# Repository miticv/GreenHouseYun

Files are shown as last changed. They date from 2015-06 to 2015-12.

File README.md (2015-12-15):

# GreenHouseYun
Green House Controller App using Arduino Yun

Command for getting public IP from network interface eth1:
```bash
LANG=c ifconfig eth1 | grep "inet addr" | awk -F: '{print $2}' | awk '{print $1}'
```
or if not sure what is the interface, list all interfaces:
```bash
LANG=c ifconfig |grep -B1 "inet addr" |awk '{ if ( $1 == "inet" ) { print $2 } else if ( $2 == "Link" ) { printf "%s:" ,$1 } }' |awk -F: '{ print $1 ": " $3 }'
```

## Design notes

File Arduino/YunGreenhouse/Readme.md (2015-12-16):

Ino is using following pins:
##ANALOG:
* 0 - read light

##DIGITAL:
* 2 - One Wire (for temperature sensors)
* 7 - Pin to reboot the Yun
* 10 - DHT Temp/Humidity Sensor (DHT22)
* 13 - built in red light on the YUN (signal when arduino is ready)

##Website: 
* http://192.168.1.35/sd/

##Arduino APIs:
It is accepting only calls from Linux box on: http://127.0.0.1:5555/

* temp  (reads temperature from DHT sensor)
* temps (reads all temperatures from sensors)
* light (reads light sensor)
* err (show last error)
* veggielightoff 
* veggielighton
* lightoff
* lighton
* boot (reboots the arduino)
* data (gets all sensor data back)

##APIs:

accepts "from" and "to"

* http://192.168.1.35/sd/api.php?action=get_info_log
* http://192.168.1.35/sd/api.php?action=get_error_log

accepts "from", "to" and "freq"

* http://192.168.1.35/sd/api.php?action=get_sensor_log
* 

* http://192.168.1.35/sd/api.php?action=light_off
* http://192.168.1.35/sd/api.php?action=light_on
* http://192.168.1.35/sd/api.php?action=get_uptime
* http://192.168.1.35/sd/api.php?action=get_sensor_data
* http://192.168.1.35/sd/api.php?action=get_sensor_definitions
* http://192.168.1.35/sd/api.php?action=get_sensor_and_uptime_data
* http://192.168.1.35/sd/api.php?action=reset_arduino
* http://192.168.1.35/sd/api.php?action=reset_yun

##BASIC WRT

* ssh root@ip.address.of.the.yun
* mysql -root -p

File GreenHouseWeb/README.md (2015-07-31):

# pluralsight-gulp
You've built your JavaScript application but how do you automate testing, code analysis, running it locally or deploying it? These redundant tasks can consume valuable time and resources. Stop working so hard and take advantage of JavaScript task automation using Gulp to streamline these tasks and give you back more time in the day. Studying this repo can help clarify how Gulp works, jump-start task automation with Gulp, find and resolve issues faster, and be a more productive.

## Requirements

- Install Node
	- on OSX install [home brew](http://brew.sh/) and type `brew install node`
	- on Windows install [chocolatey](https://chocolatey.org/) 
    - Read here for some [tips on Windows](http://jpapa.me/winnode)
    - open command prompt as administrator
        - type `choco install nodejs`
        - type `choco install nodejs.install`
- On OSX you can alleviate the need to run as sudo by [following these instructions](http://jpapa.me/nomoresudo). I highly recommend this step on OSX
- Open terminal
- Type `npm install -g node-inspector bower gulp`

## Quick Start
Prior to taking the course, clone this repo and run the content locally
```bash
$ npm install
$ bower install
$ npm start    (or: $ node src/server/server.js)
```
## Gulp, bower and npm

npm installs server packages( -g installs it globaly)
```bash
  npm install -g gulp bower
```
 list to show all global packages installed:
```bash
  npm list -g --depth=0 
```
--save saves to dependencies in package.json (run time dependencies: angular, bootstrap, ...)
```bash
  npm install --save
```
--save-dev saves in devDEpendencies in package.json (developer dependencies: JSHint, Uglify, Concat...)
```bash
  npm install --save-dev
```
## bower client packages

```bash
npm install -g gulp bower
```
#js
```bash
npm install --save-dev gulp-jscs gulp-jshint yargs gulp-load-plugins gulp-if gulp-print gulp-util jshint-stylish 
```
#css
```bash
npm install --save-dev gulp-less gulp-autoprefixer del gulp-plumber
```
#html
```bash
npm install --save-dev gulp-inject wiredep
```
#Automated starting dev:
```bash
npm install --save-dev gulp-nodemon
```bash

#browser syncing
```bash
npm install --save-dev browser-sync
```

# build

```bash
npm install --save-dev gulp-task-listing gulp-imagemin
```

gulp angular template cache
```bash
npm install --save-dev gulp-minify-html gulp-angular-templatecache

npm install --save-dev gulp-useref

npm install --save-dev gulp-csso gulp-uglify gulp-filter
```

# Angular automated anotation 

Finds code and adds annotation:
```bash
npm install --save-dev gulp-ng-annotate
```
now we can just write: 
```bash
  controller('homeController', function ($scope, greenApiService, NotifierService, $q, $interval) 
```
instead of:
```bash
  controller('homeController', ['$scope', 'greenApiService', 'NotifierService', '$q', '$interval',
                       function ($scope, greenApiService, NotifierService, $q, $interval) 
```
or:
```bash
  controller('homeController', homeController);
 function homeController($scope, greenApiService, NotifierService, $q, $interval) 
```
instead of:
```bash
  controller('homeController', homeController);
  homeController.$inject ['$scope', 'greenApiService', 'NotifierService', '$q', '$interval'];
  function  homeController($scope, greenApiService, NotifierService, $q, $interval) 
```

# revisions

```bash
npm install --save-dev gulp-rev gulp-rev-replace gulp-bump
```

# testing with karma

```bash
npm install --save-dev mocha chai sinon
npm install --save-dev karma karma-chai karma-chai-sinon karma-chrome-launcher karma-coverage karma-growl-reporter karma-mocha karma-phantomjs-launcher karma-sinon mocha-clean sinon-chai phantomjs
npm install --save-dev karma-ie-launcher
```
npm WARN deprecated mocha-clean@0.4.0: Mocha 2.2.5 already shortens stack traces by default.

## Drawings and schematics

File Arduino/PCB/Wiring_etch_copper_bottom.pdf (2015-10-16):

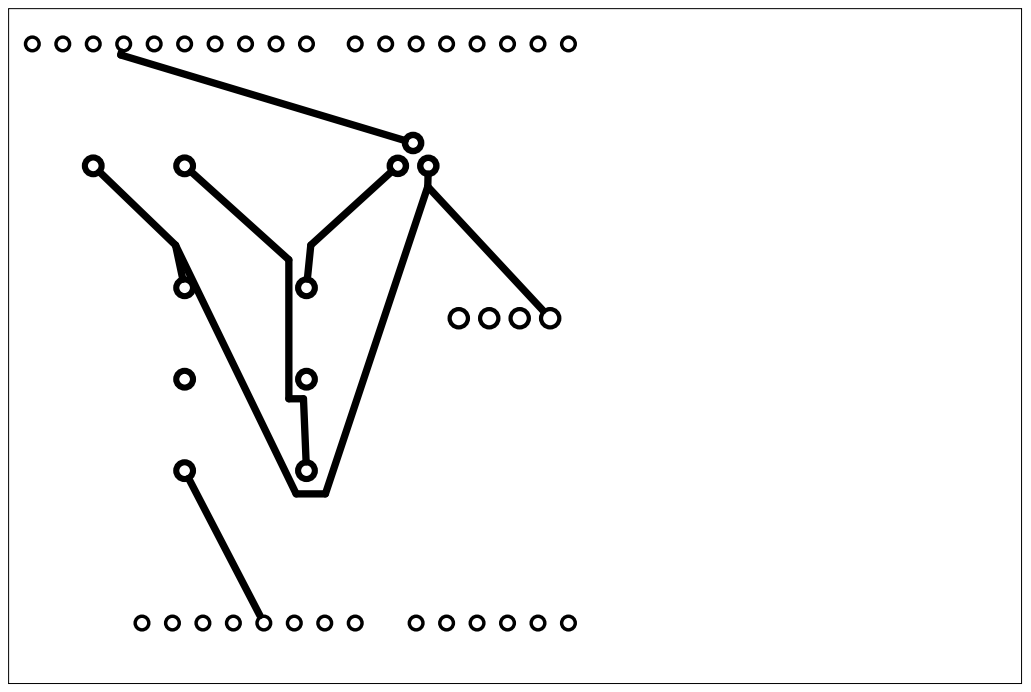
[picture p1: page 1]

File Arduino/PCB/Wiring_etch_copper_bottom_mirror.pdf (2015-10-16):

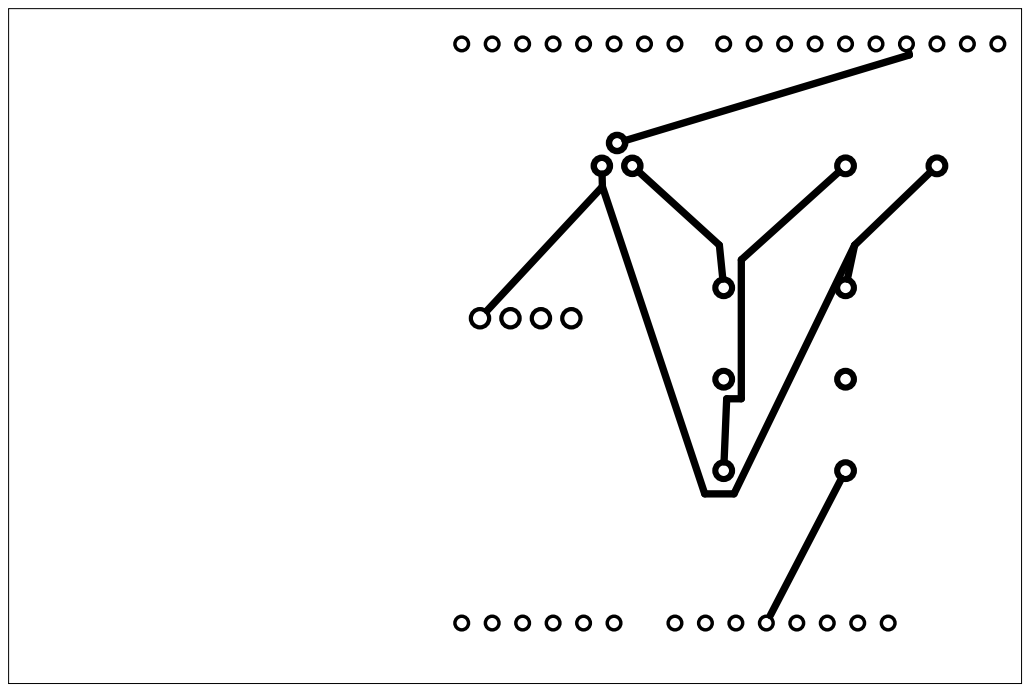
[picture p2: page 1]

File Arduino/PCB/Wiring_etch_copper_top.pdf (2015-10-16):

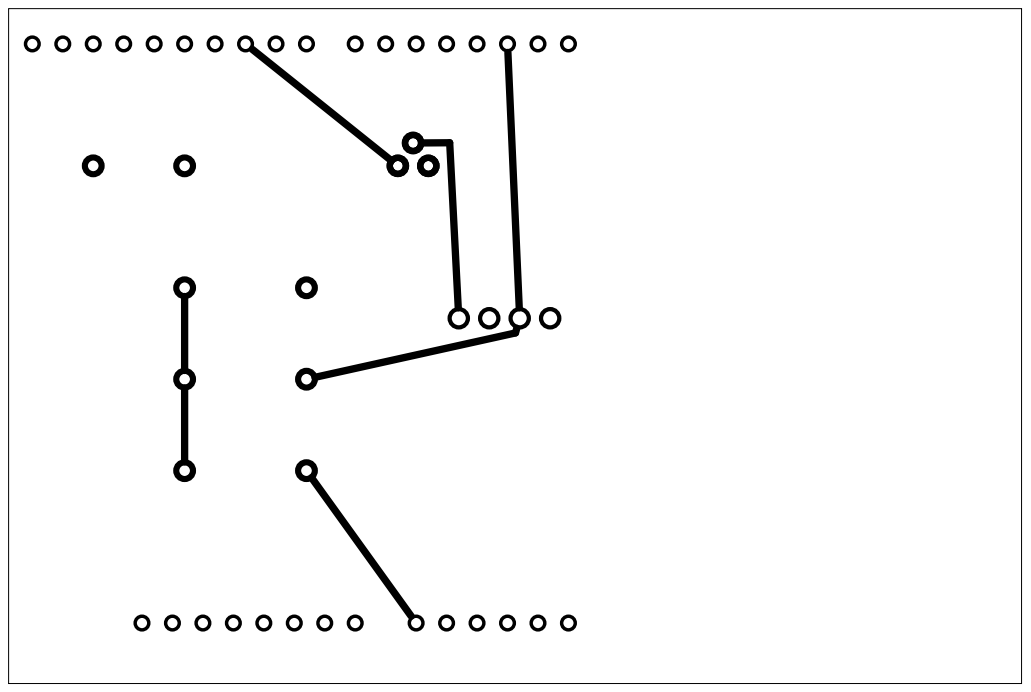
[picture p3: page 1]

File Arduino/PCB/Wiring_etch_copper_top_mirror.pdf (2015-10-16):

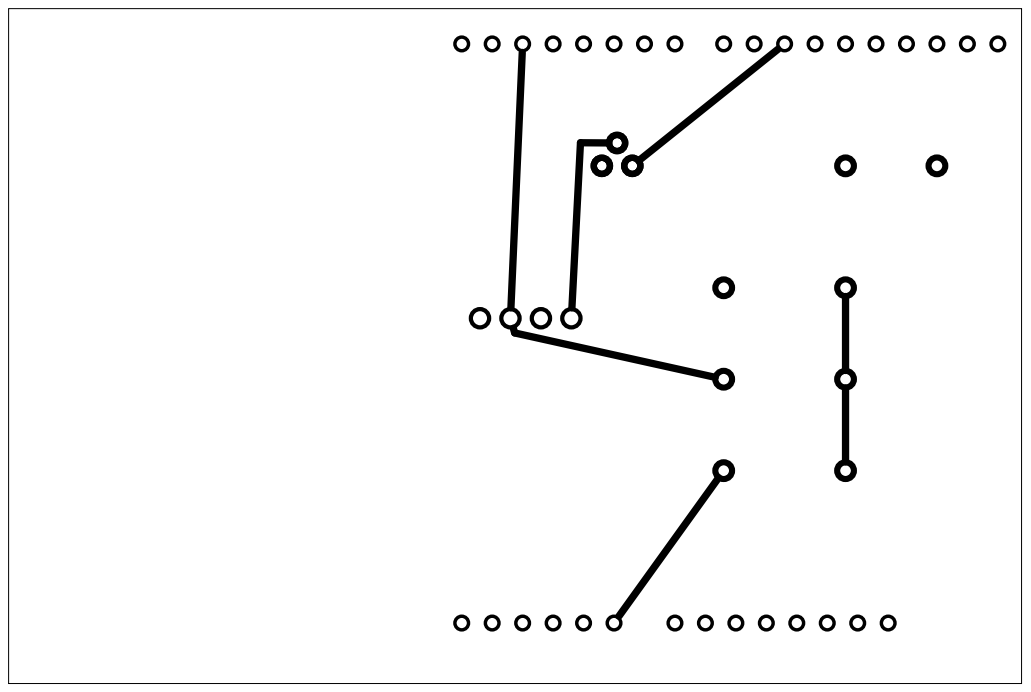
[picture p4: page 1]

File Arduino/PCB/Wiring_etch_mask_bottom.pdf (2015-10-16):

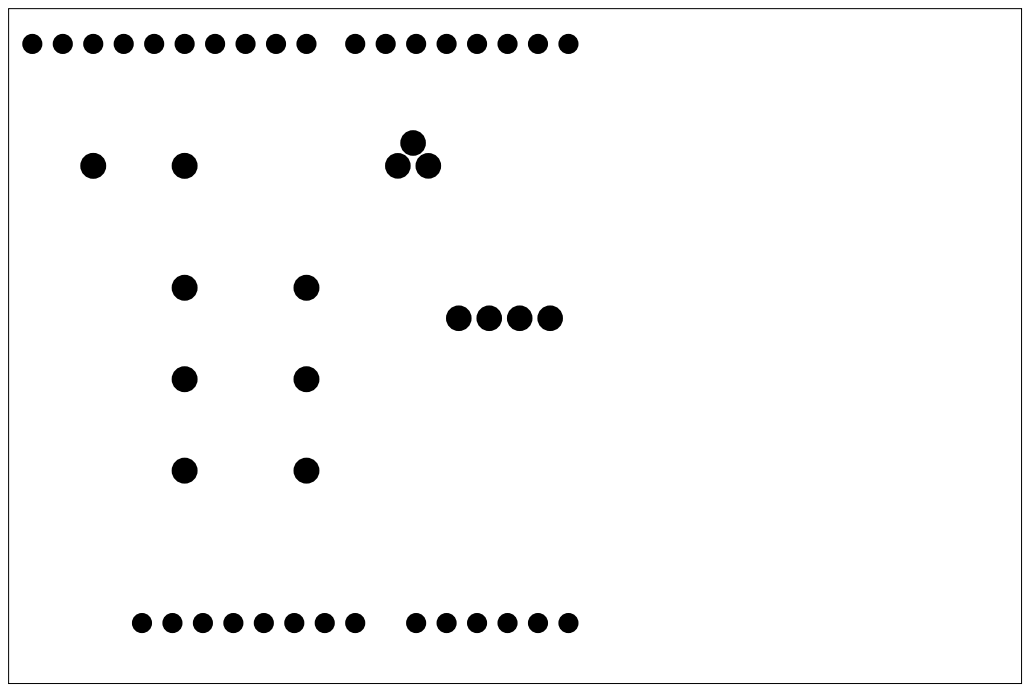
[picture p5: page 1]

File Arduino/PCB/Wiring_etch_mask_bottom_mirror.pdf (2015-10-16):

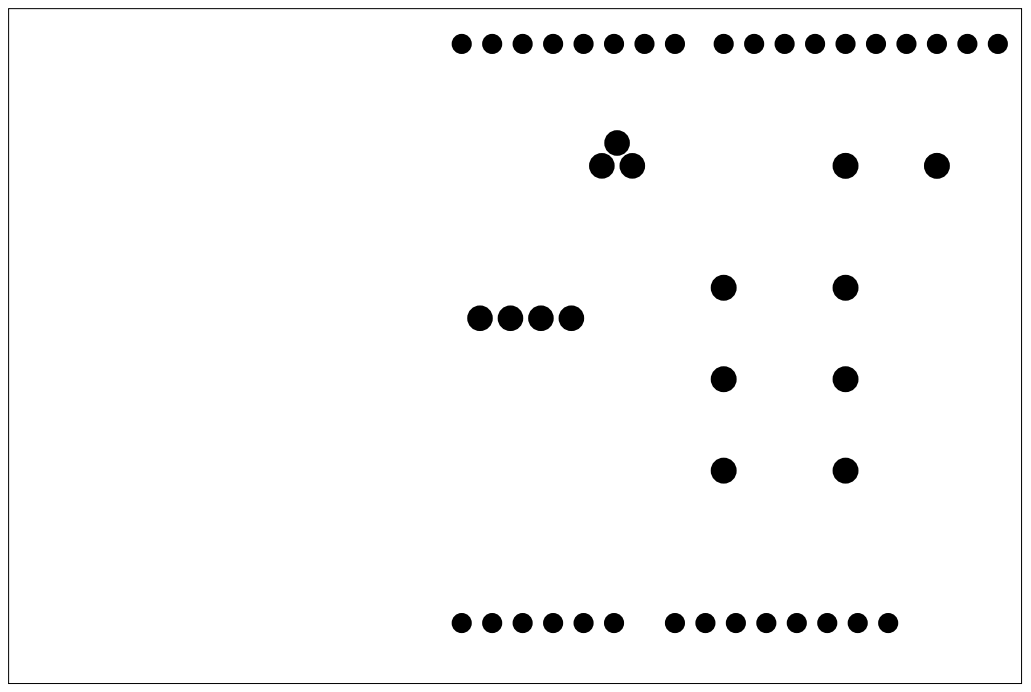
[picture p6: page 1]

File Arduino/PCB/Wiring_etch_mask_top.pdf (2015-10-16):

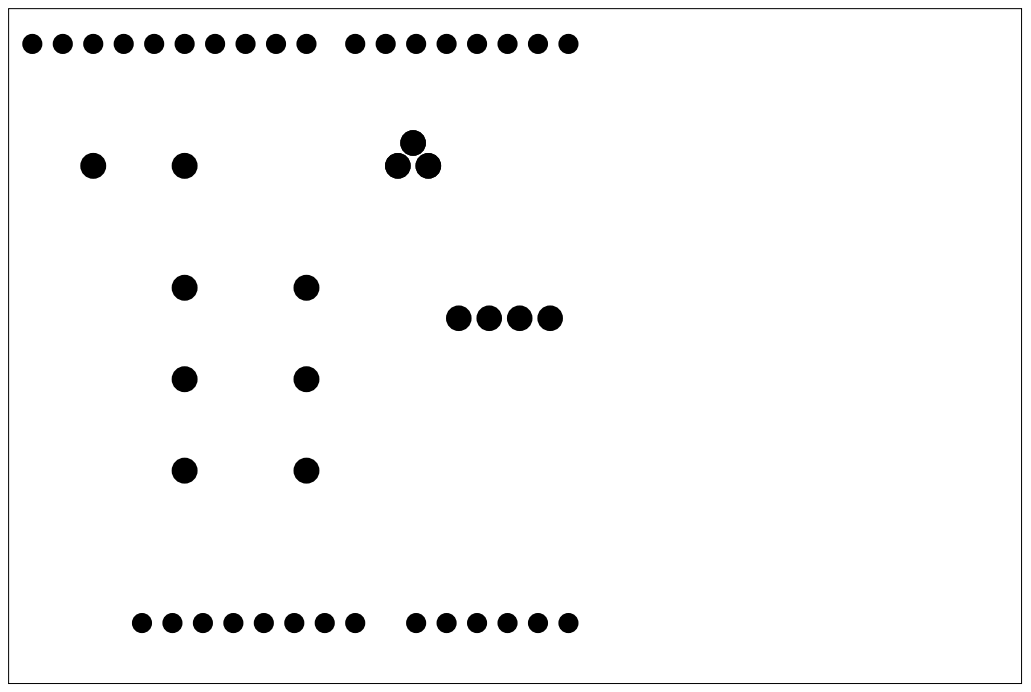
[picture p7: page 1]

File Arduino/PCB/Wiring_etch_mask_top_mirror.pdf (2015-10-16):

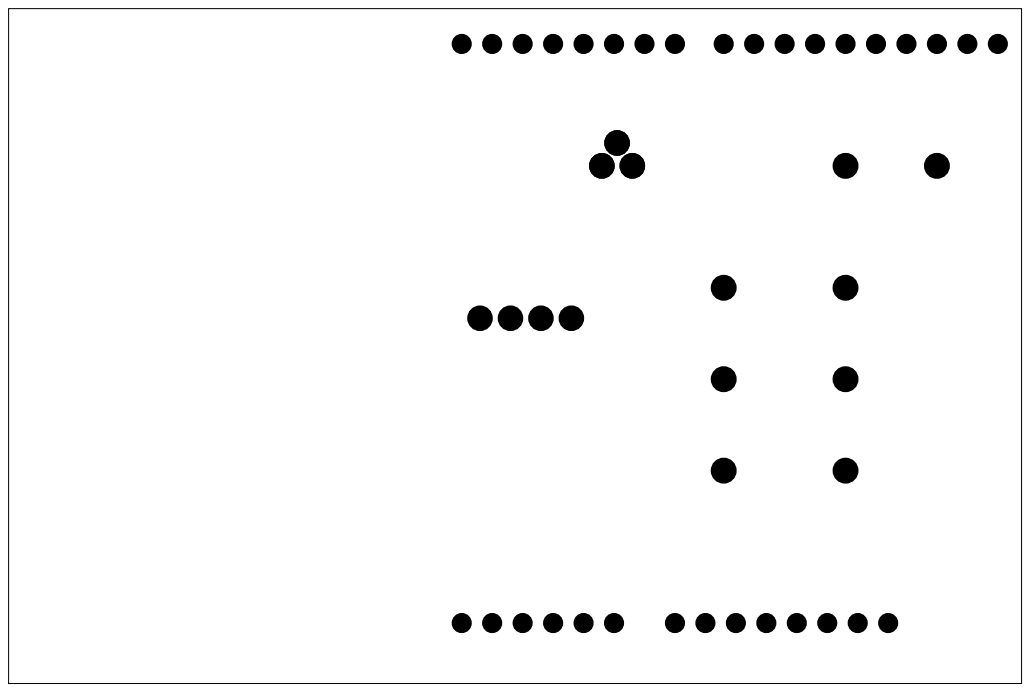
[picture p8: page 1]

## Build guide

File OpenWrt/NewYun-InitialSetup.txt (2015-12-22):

1) do YunSysupgrade:
http://www.arduino.cc/en/Tutorial/YunSysupgrade
- Get SD card (2GB)
- Copy to root the openwrt-ar71xx-generic-yun-16M-squashfs-sysupgrade.bin
- Connect to YUN wifi
- open http://192.168.240.1
- Default password is "arduino"
- Click "RESET" button

2) expand YUN disk space:
http://www.arduino.cc/en/Tutorial/ExpandingYunDiskSpace
- Upload the sketch "YunDiskSpaceExpander.ino" using serial connection
- Open Serial monitor (using NewLine dropdown menu)
- yes (proceed)
- yes (connected to internet)
- yes (partitioning - will loose everything from the SD card)
- 1024 (size in MB for partition)
- When done press YUN RST to reboot

3) check system:
df -h / /mnt/sda1

=================================================================================

1ALT) ALTERNATIVE WITHOUT WEB INTERFACE (with latest linino):
	cd /mnt/sda1
	wget http://download.linino.org/linino_distro/master/latest/openwrt-ar71xx-generic-linino-yun-16M-250k-squashfs-sysupgrade.bin
	sysupgrade -v openwrt-ar71xx-generic-linino-yun-16M-250k-squashfs-sysupgrade.bin
	NOTE:
	above version is not 100% yun compatible better FTP this file to sd card and install that one:
	openwrt-ar71xx-generic-yun-16M-squashfs-sysupgrade.bin
	How to set up ftp? view here https://github.com/miticv/GreenHouseYun/blob/master/OpenWrt/SetUpScript.txt

2ALT) AlTERNATIVE without INO and serial connection:
a)haltIfSDAlreadyOnOverlay 
(should give no results, if it does: Micro SD card is already used as additional Arduino Yun disk space. Nothing to do.)
	mount | grep ^/dev/sda | grep 'on /overlay'
	
b)haltIfInternalFlashIsFull
should give more than 1000 otherwise: You don't have enough disk space to install the utility software. You need to free at least 1MB of Flash memory.\nRetry!
	df / | awk '/rootfs/ {print $4}'
		
c)haltIfSDCardIsNotPresent
(should list - make sure SD card is in "The micro SD card is not available")
	ls /mnt/sda1

d)installSoftware
//make sure you are online:
	opkg update
	opkg install e2fsprogs mkdosfs fdisk rsync

//if Signature check failed.Remove wrong Signature file. then comment #option check_signature from /etc/opkg.conf

e)partitionAndFormatSDCard

//unmount
	umount /dev/sda?
	rm -rf /mnt/sda?

//clears partition table
	dd if=/dev/zero of=/dev/sda bs=4096 count=10

// create the first partition (replace 1024 to how many megs you want for data)
	(echo n; echo p; echo 1; echo; echo +2048M; echo w) | fdisk /dev/sda

//unmount
	umount /dev/sda?
	rm -rf /mnt/sda?

// create the second partition
	(echo n; echo p; echo 2; echo; echo; echo w) | fdisk /dev/sda

//unmount
	umount /dev/sda?
	rm -rf /mnt/sda?

// specify first partition is FAT32
	(echo t; echo 1; echo c; echo w) | fdisk /dev/sda

//unmount
	umount /dev/sda?
	rm -rf /mnt/sda?

// wait 5 sec
//unmount
	umount /dev/sda?
	rm -rf /mnt/sda?

// format the first partition to FAT32
	mkfs.vfat /dev/sda1

// wait 1 sec

// format the second partition to Linux EXT4
	mkfs.ext4 /dev/sda2

f)createArduinoFolder

	mkdir -p /mnt/sda1
	mount /dev/sda1 /mnt/sda1
	mkdir -p /mnt/sda1/arduino/www
//unmount
	umount /dev/sda?
	rm -rf /mnt/sda?

g)copySystemFilesFromYunToSD
	
	mkdir -p /mnt/sda2
	mount /dev/sda2 /mnt/sda2
	rsync -a --exclude=/mnt/ --exclude=/www/sd /overlay/ /mnt/sda2/
//unmount
	umount /dev/sda?
	rm -rf /mnt/sda?

h)enableExtRoot

	uci add fstab mount
	uci set fstab.@mount[0].target=/overlay
	uci set fstab.@mount[0].device=/dev/sda2
	uci set fstab.@mount[0].fstype=ext4
	uci set fstab.@mount[0].enabled=1
	uci set fstab.@mount[0].enabled_fsck=0
	uci set fstab.@mount[0].options=rw,sync,noatime,nodiratime
	uci commit

i) We are done! Now press the YUN RST button to apply the changes.

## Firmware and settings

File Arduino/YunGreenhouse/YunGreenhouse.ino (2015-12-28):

#include <Bridge.h>
#include <YunServer.h>
#include <YunClient.h> 
#include <Process.h>  /* for making OpenWrt linux process requests */

YunServer server;
YunClient client;

/* ##################### temperature humidity ##################### */
#include "DHT.h"
#define DHTPIN 10        // what pin we're connected to DIGITAL


// Uncomment whatever type you're using!
//#define DHTTYPE DHT11   // DHT 11 
#define DHTTYPE DHT22   // DHT 22  (AM2302)
//#define DHTTYPE DHT21   // DHT 21 (AM2301)

// Connect pin 1 (on the left) of the sensor to +5V
// NOTE: If using a board with 3.3V logic like an Arduino Due connect pin 1
// to 3.3V instead of 5V!
// Connect pin 2 of the sensor to whatever your DHTPIN is
// Connect pin 4 (on the right) of the sensor to GROUND
// Connect a 10K resistor from pin 2 (data) to pin 1 (power) of the sensor

// Initialize DHT sensor for normal 16mhz Arduino
DHT dht(DHTPIN, DHTTYPE);
// NOTE: For working with a faster chip, like an Arduino Due or Teensy, you
// might need to increase the threshold for cycle counts considered a 1 or 0.
// You can do this by passing a 3rd parameter for this threshold.  It's a bit
// of fiddling to find the right value, but in general the faster the CPU the
// higher the value.  The default for a 16mhz AVR is a value of 6.  For an
// Arduino Due that runs at 84mhz a value of 30 works.
// Example to initialize DHT sensor for Arduino Due:
//DHT dht(DHTPIN, DHTTYPE, 30);

/* ##################### resetFunc ################################ */
void(*resetFunc) (void) = 0;  //declare reset function @ address 0


/* ##################### temperature libraries ##################### */
#include <OneWire.h>
#include <DallasTemperature.h>

#define ONEWIREPIN 2  // what pin we're connected to DIGITAL
OneWire bus(ONEWIREPIN);
DallasTemperature sensors(&bus);
const int TemperatureDevices = 10;
int numberOfDevices;
DeviceAddress tempSensors[TemperatureDevices];  //DeviceAddress is uint8_t[8]
bool tempSensorsReadable[TemperatureDevices];

/* ############################### boot ########################### */
#define BOOTPIN 7        // what pin we're connected to DIGITAL BOOT (default closed: HIGH)

/* ############################### digital pins ########################### */
#define VEGGIEPIN 6        // what pin we're connected to VEGGIE LIGHT  (default closed: HIGH)
#define LIGHTPIN 5              // what pin we're connected to GreenhouseLight  (default closed: HIGH)
#define BRIDGEREADYPIN 13     ////light up LED 13 as a signal that bridge is ready

/* ############################### analog pins ########################### */
#define LIGHTSENSORPIN 0    //
/* ##################### VARS ##################################### */
// All request will be transfered here
float TempVar[4];
int i;
char errorString[50];
char tempString[100];
char temp;
//char sensorFloatValue[10];
char sensorValue[5];
Process p;
String command;
 
void setup() {
// Bridge startup: 
  // do nothing for 10 seconds (do not interupt booting process):
  delay(10000); 

  pinMode(BOOTPIN, OUTPUT);
  digitalWrite(BOOTPIN, HIGH);

  pinMode(VEGGIEPIN, OUTPUT);
  digitalWrite(VEGGIEPIN, HIGH);

  pinMode(LIGHTPIN, OUTPUT);
  digitalWrite(LIGHTPIN, HIGH);
  
  pinMode(BRIDGEREADYPIN, OUTPUT);
  digitalWrite(BRIDGEREADYPIN, LOW);

  Bridge.begin();

  dht.begin();
  
  sensors.begin();
  SensorsSetUp();
  
  //asks for credentials:
  server.noListenOnLocalhost(); 
  //does not ask for credentials:
  //server.listenOnLocalhost();
  
  server.begin();
  
  //light up LED 13 as a signal that bridge is ready
  digitalWrite(BRIDGEREADYPIN, HIGH);
 
}

void loop() {
  
  // Get clients coming from server
  client = server.accept();
  // There is a new client?
  if (client) {
        // read the command
        getCommand();
        
	clientSendJSON();

	if (command == "temp") {
		ReadDHT();
	}
	else if (command == "temps") {
		ReadTemps();
	}
	else if (command == "light") {
		ReadLight();
	}
	else if (command == "err") {
		ShowLastError();
	}
	else if (command == "veggielightoff") {
		VeggieLight(0);
	}
	else if (command == "veggielighton") {
		VeggieLight(1);
	}
	else if (command == "lightoff") {
		Light(1);
	}
	else if (command == "lighton") {
		Light(0);
	}
  else if (command == "lightflick") {
    if(digitalRead(LIGHTPIN) == HIGH){
        Light(0);
    }else{
        Light(1);
    }
  }
	else if (command == "boot") {
		Reboot();
	}
	else if (command == "data") {
		ReadData();
	}else{
          client.println("{\"error\":\"Invalid command\" }");
        }

    // Close connection and free resources.
    client.stop();
    
  }
  digitalWrite(13, HIGH);
  delay(50); // Poll every 50ms
       
}

void ReadData(){
	client.print("{ \"Light\": ");
	ReadLight();
	client.print(", \"DHT\": ");
	ReadDHT();
	client.print(", \"Temperatures\": ");
	ReadTemps();
	client.print(", \"DigitalPins\": ");
	ReadDigitalPins();

	        client.print(", \"NumberOfTemperatures\": ");
			client.print(numberOfDevices);

//        client.print(", \"Command\": ");
//        client.print("\"");
//        client.print(command);
//        client.print("\"");

	client.print("}");
}

void ReadLight(){

	// Measure light level: LIGHTSENSORPIN
	client.print("{ \"Light\":");
	client.print(analogRead(LIGHTSENSORPIN));
	client.print(", \"Address\": \"Analog");
	client.print(LIGHTSENSORPIN);
	client.print("\"");
	client.print(" }");
}

void ReadDHT(){

	// Reading temperature or humidity takes about 250 milliseconds!
	// Sensor readings may also be up to 2 seconds 'old' (its a very slow sensor)
	TempVar[0] = dht.readHumidity();
	// Read temperature as Celsius
	TempVar[1] = dht.readTemperature();
	// Read temperature as Fahrenheit
	TempVar[2] = dht.readTemperature(true);
	// Check if any reads failed and exit early (to try again).
	if (isnan(TempVar[0]) || isnan(TempVar[1]) || isnan(TempVar[2])) {
		client.print("{\"error\":\"Failed to read from DHT sensor!\"}");
	}
	else{
		// Compute heat index
		// Must send in temp in Fahrenheit!
		TempVar[3] = dht.computeHeatIndex(TempVar[2], TempVar[0]);

		client.print("{ \"HumidityPercent\":");
		client.print(TempVar[0]);
		client.print(", \"TempC\":");
		client.print(TempVar[1]);
		client.print(", \"TempF\":");
		client.print(TempVar[2]);
		client.print(" , \"HeatIndexF\":");
		client.print(TempVar[3]);
		client.print(", \"Address\": \"Digital");
		client.print(DHTPIN);
		client.print("\"");
		client.print("}");

	}
}

void ReadTemps(){

	sensors.requestTemperatures();
	client.print("[");
	for (i = 0; i < numberOfDevices; i++)
	{		
		client.print("{ \"Address\": \"");
		printAddress(tempSensors[i]);
		client.print("\" ,");
		client.print("\"TempC\": ");		
		if (tempSensorsReadable[i]){ 
			TempVar[0] = sensors.getTempC(tempSensors[i]);
			if (TempVar[0] < -100){  //sensor disconnected shows -127
				client.print("-999");
			}
			else{
				client.print(TempVar[0]);
			}			
		}
		else {
			client.print("-999");
		}
		client.print("}");
		if (i != (numberOfDevices - 1)) client.print(", ");
	}
	client.print("]");
}

void ReadDigitalPins(){
	
	client.print("{ ");
	client.print("\"VeggieLight\": { \"value\": ");
	client.print(digitalRead(VEGGIEPIN));
	client.print(", \"Address\": \"Digital");
	client.print(VEGGIEPIN);
	client.print("\" },");

	client.print("\"Light\": {  \"value\":");
	client.print(digitalRead(LIGHTPIN));
	client.print(", \"Address\": \"Digital");
	client.print(LIGHTPIN);
	client.print("\" }");
	client.print("} ");
}

void ShowLastError(){

	client.print("{ \"error\" : \"");
	client.print(errorString);
	client.print("\"}");

}

void Reboot(){
  digitalWrite(BOOTPIN, LOW); //send reboot signal
}

void VeggieLight(uint8_t onoff){
	if (onoff == 0){
		digitalWrite(VEGGIEPIN, LOW);
		client.print("{ \"result\" : \"success veggie light low\" }");
	}
	else {
		digitalWrite(VEGGIEPIN, HIGH);
		client.print("{ \"result\" : \"success  veggie light high\" }");
	}
}

void Light(uint8_t onoff){
	if (onoff == 0){
		digitalWrite(LIGHTPIN, LOW);
		client.print("{ \"result\" : \"success light low\" }");
	}
	else {
		digitalWrite(LIGHTPIN, HIGH);
		client.print("{ \"result\" : \"success light high\" }");
	}
}

void clientSendJSON(){
	client.println("Status: 200");
	client.println("Content-type: application/json");
	client.println();
}

void getCommand(){
        //String command = client.readString();
        int i = 0;
        while(command.indexOf("GET") < 0 || i > 20 ){
                command = client.readStringUntil('\r');
                i++;
        }
        command.trim();        //kill whitespace
        command = command.substring(command.indexOf(" /")+2,command.indexOf(" HTTP"));  //"GET /data HTTP/1.1"
}

void SensorsSetUp(){

	numberOfDevices = sensors.getDeviceCount();

	for (i = 0; i < numberOfDevices; i++)
	{
		strcpy(errorString, "DS18B20 not found: ");
		if (!sensors.getAddress(tempSensors[i], i))
		{
			tempSensorsReadable[i] = false;
			strcat(errorString, itoa(i + 1, sensorValue, 10));
			strcat(errorString, " ");
		}
		else{
			tempSensorsReadable[i] = true;
		}
	}


}

void printAddress(uint8_t* address){

	for (int j = 0; j < 8; j++)
	{
		client.print(address[j], HEX);
		if(j<7) client.print(" ");
	}

}

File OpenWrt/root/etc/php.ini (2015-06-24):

[PHP]

zend.ze1_compatibility_mode = Off

; Language Options

engine = On
;short_open_tag = Off
precision    =  12
y2k_compliance = On
output_buffering = Off
;output_handler =
zlib.output_compression = Off
;zlib.output_compression_level = -1
;zlib.output_handler =
implicit_flush = Off
unserialize_callback_func =
serialize_precision = 100

;open_basedir =
disable_functions =
disable_classes =

; Colors for Syntax Highlighting mode.  Anything that's acceptable in
; <span style="color: ???????"> would work.
;highlight.string  = #DD0000
;highlight.comment = #FF9900
;highlight.keyword = #007700
;highlight.bg      = #FFFFFF
;highlight.default = #0000BB
;highlight.html    = #000000

;ignore_user_abort = On
;realpath_cache_size = 16k
;realpath_cache_ttl = 120

; Miscellaneous

expose_php = On

; Resource Limits

max_execution_time = 30	; Maximum execution time of each script, in seconds.
max_input_time = 60	; Maximum amount of time each script may spend parsing request data.
;max_input_nesting_level = 64
memory_limit = 8M	; Maximum amount of memory a script may consume.

; Error handling and logging

; Error Level Constants:
; E_ALL             - All errors and warnings (includes E_STRICT as of PHP 6.0.0)
; E_ERROR           - fatal run-time errors
; E_RECOVERABLE_ERROR  - almost fatal run-time errors
; E_WARNING         - run-time warnings (non-fatal errors)
; E_PARSE           - compile-time parse errors
; E_NOTICE          - run-time notices (these are warnings which often result
;                     from a bug in your code, but it's possible that it was
;                     intentional (e.g., using an uninitialized variable and
;                     relying on the fact it's automatically initialized to an
;                     empty string)
; E_STRICT			- run-time notices, enable to have PHP suggest changes
;                     to your code which will ensure the best interoperability
;                     and forward compatibility of your code
; E_CORE_ERROR      - fatal errors that occur during PHP's initial startup
; E_CORE_WARNING    - warnings (non-fatal errors) that occur during PHP's
;                     initial startup
; E_COMPILE_ERROR   - fatal compile-time errors
; E_COMPILE_WARNING - compile-time warnings (non-fatal errors)
; E_USER_ERROR      - user-generated error message
; E_USER_WARNING    - user-generated warning message
; E_USER_NOTICE     - user-generated notice message
; E_DEPRECATED      - warn about code that will not work in future versions
;                     of PHP
; E_USER_DEPRECATED - user-generated deprecation warnings
;
; Common Values:
;   E_ALL & ~E_NOTICE  (Show all errors, except for notices and coding standards warnings.)
;   E_ALL & ~E_NOTICE | E_STRICT  (Show all errors, except for notices)
;   E_COMPILE_ERROR|E_RECOVERABLE_ERROR|E_ERROR|E_CORE_ERROR  (Show only errors)
;   E_ALL | E_STRICT  (Show all errors, warnings and notices including coding standards.)
; Default Value: E_ALL & ~E_NOTICE
error_reporting  =  E_ALL & ~E_NOTICE & ~E_STRICT

display_errors = On
display_startup_errors = Off
log_errors = Off
log_errors_max_len = 1024
ignore_repeated_errors = Off
ignore_repeated_source = Off
report_memleaks = On
;report_zend_debug = 0
track_errors = Off
;html_errors = Off
;docref_root = "/phpmanual/"
;docref_ext = .html
;error_prepend_string = "<font color=#ff0000>"
;error_append_string = "</font>"
; Log errors to specified file.
;error_log = /var/log/php_errors.log
; Log errors to syslog.
;error_log = syslog

; Data Handling

;arg_separator.output = "&amp;"
;arg_separator.input = ";&"
variables_order = "EGPCS"
request_order = "GP"
register_globals = Off
register_long_arrays = Off
register_argc_argv = On
auto_globals_jit = On
post_max_size = 8M
;magic_quotes_gpc = Off
magic_quotes_runtime = Off
magic_quotes_sybase = Off
auto_prepend_file =
auto_append_file =
default_mimetype = "text/html"
;default_charset = "iso-8859-1"
;always_populate_raw_post_data = On

; Paths and Directories

; UNIX: "/path1:/path2"
;include_path = ".:/php/includes"
doc_root = "/www"
user_dir =
extension_dir = "/usr/lib/php"
enable_dl = On
;cgi.force_redirect = 1
;cgi.nph = 1
;cgi.redirect_status_env = ;
cgi.fix_pathinfo=1
;fastcgi.impersonate = 1;
;fastcgi.logging = 0
;cgi.rfc2616_headers = 0

; File Uploads

file_uploads = On
upload_tmp_dir = "/tmp"
upload_max_filesize = 2M
max_file_uploads = 20

; Fopen wrappers

allow_url_fopen = On
allow_url_include = Off
;from="john@doe.com"
;user_agent="PHP"
default_socket_timeout = 60
;auto_detect_line_endings = Off

; Dynamic Extensions
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

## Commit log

2015-06-11 arduino/temp api (humidity and 2 temp sensors) working
2015-06-21 Temperatures and Humidity api working from arduino :)
2015-06-21 fix reading when sensor fails
    [YunGreenhouse.ino]
2015-06-21 dynamically adds up to 10 temperature sensors and showing addresses as well
2015-06-22 Date api Fritz diagram
    [Wiring.fzz, WiringBoard.fzz]
2015-06-24 remove api from arduino for linux alive time
2015-06-26 Showing temperatures 1-5 to website
2015-07-02 Added device backup file
2015-07-02 Scripts for logging sensors (in progress)
2015-07-03 log sensors
2015-07-07 Logging the sensor data to database now
2015-07-11 completed php apis, simplified arduino code (move some apis to php instead)
2015-07-11 Moved reset api to php api
    [YunGreenhouse.ino]
2015-07-13 Added sensor definitions
2015-07-13 Added new API to show sensor names
2015-08-03 Added graph - current month temperatures
2015-08-04 Filtering done for graph history
2015-10-14 server now serves Json files for local testing
    [Wiring.fzz]
2015-10-15 Moved Expander in its own folder so that can be uploaded straight from there (Arduino requirement)
2015-10-16 Updated notes for brand new YUN setup
    [Wiring.fzz]
2015-11-28 Added digital pin 7 - to reboot YUN Added api to reboot Yun (not on website UI yet, have to know to manually call it) Fix Yun client to read GET command properly. Fix python TEST case
    [YunGreenhouse.ino]
2015-12-14 Adjust values of the sensors when value fails - so that graph is still readable.
2015-12-22 Update SetUpScript.txt
    Don't forget to update date time on new device
2015-12-22 Add debug values for temperature sensors
2015-12-28 Fix veggie light to work automatically Add api to flick the greenhouse light
    [YunGreenhouse.ino]
